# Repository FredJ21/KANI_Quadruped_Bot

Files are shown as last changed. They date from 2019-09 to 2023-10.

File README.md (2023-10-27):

# KANI_Quadruped_Bot
KANI - The quadruped bot

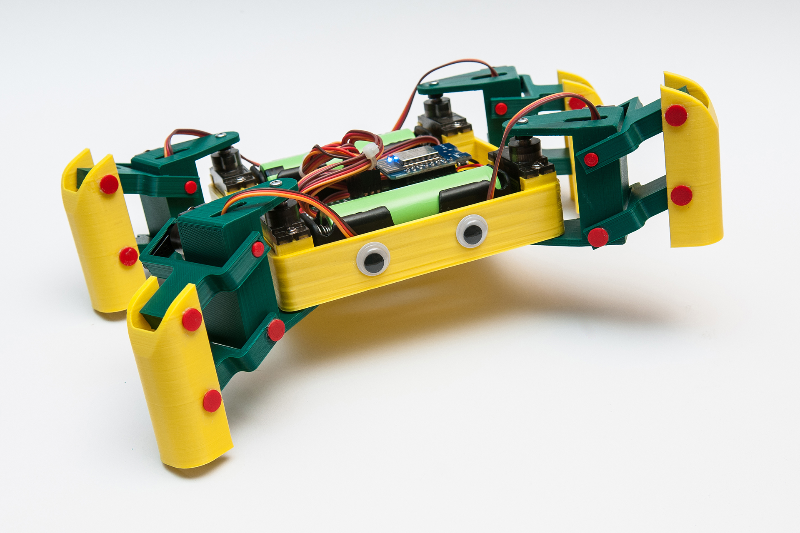
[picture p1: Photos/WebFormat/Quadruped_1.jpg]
KANI


KANI is a close cousin of KAME, another quadruped robot that we can discover here :  https://www.thingiverse.com/thing:1265766
 A big thank-you at bbq3D (https://www.thingiverse.com/bq3D/about) for his project and his inspiration.

But, KANI project is characterized by some interesting notes :

--> All the parts have been completely redesigned to facilitate 3D printing :
in PLA,

- without support structure,
- without adhesion border

--> The source files are available in the format :
- f3d  (Autodesk Fusion360)
- obj (3D format for import/export)
- stl (for 3D printing)

--> Any screws aren't needed for mounting articulation

--> The robot is designed around a ESP8266 and 8 servo motors type MG90S, in metal, robust and cheap

--> The set is powered by 2 batteries NCR18650B 3,7V 3400mAh and a 5V UBEC regulator

---
Update Sep. 2022 : BIG KANI - new version with MG996 servo

---
# On YouTube

<a href="https://youtu.be/avMEU6TQdt8">
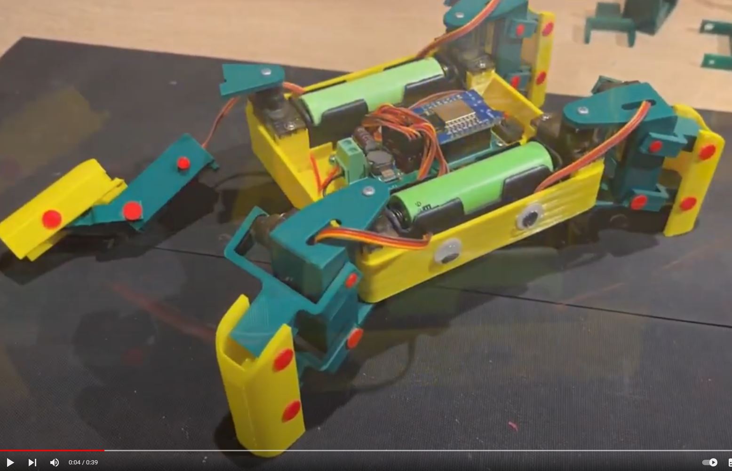
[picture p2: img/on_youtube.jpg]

</a>

https://youtu.be/avMEU6TQdt8

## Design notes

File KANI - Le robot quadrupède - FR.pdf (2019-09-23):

# KANI

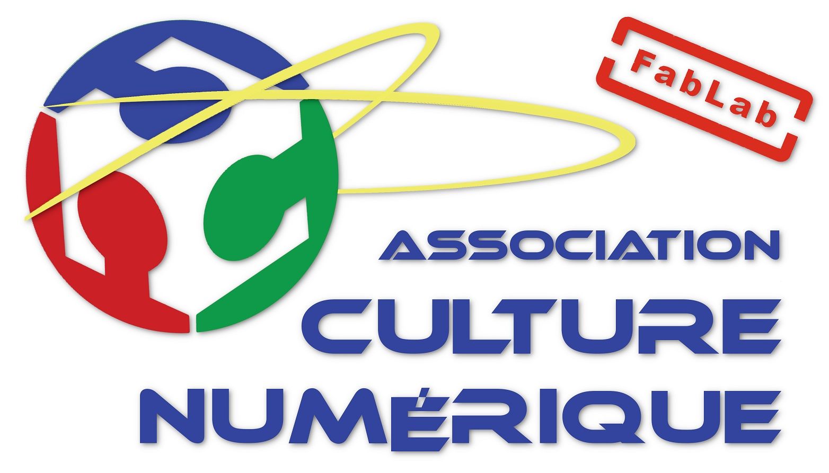
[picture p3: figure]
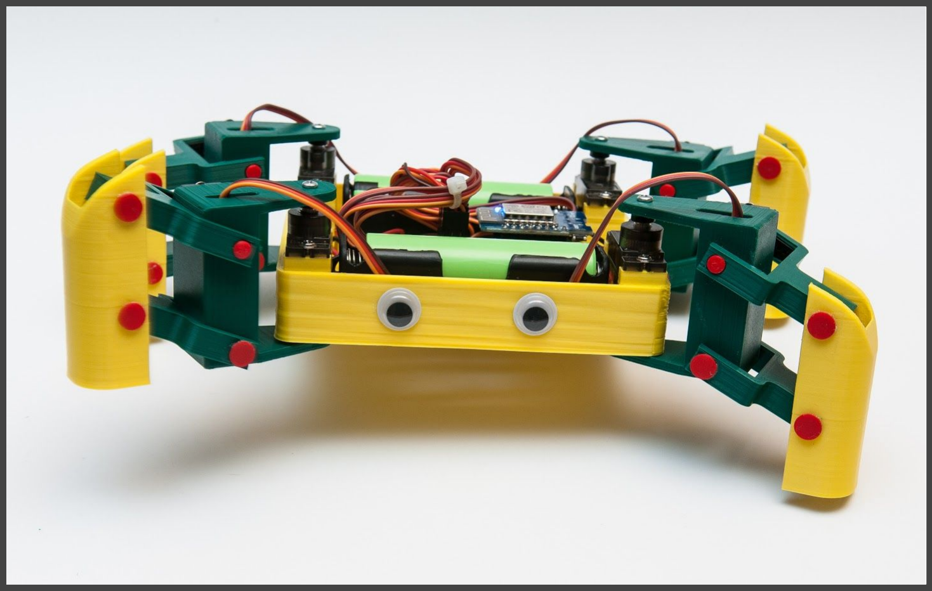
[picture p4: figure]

Le robot Quadrupède

Frédéric JELMONI
Septembre 2019

Version 1.0

# Sommaire

Présentation | 3
Réalisation des pièces mécaniques | 4
Liste des pièces | 4
Préparation des pièces | 5
Assemblage des jambes | 6
Réalisation Électronique | 8
Liste des pièces | 8
Schéma | 9
Réalisation du circuit | 10
Raccordement des moteurs | 11

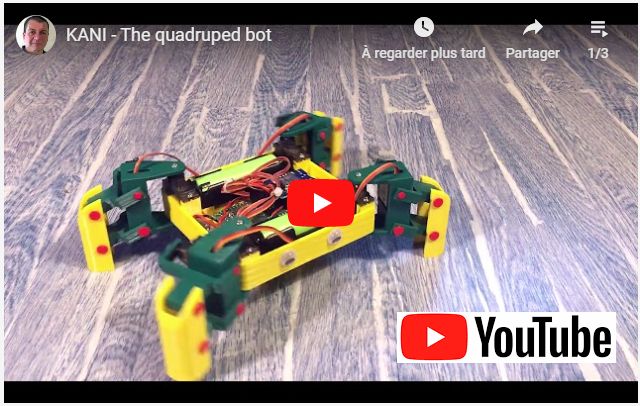
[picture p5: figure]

https://www.youtube.com/playlist?list=PLPA2ZF9G4l-84z5ALzUFqm6Zu1bBUUEop

### Présentation

KANI est un proche cousin de KAME, autre robot quadrupède que l’on peut découvrir ici : https://www.thingiverse.com/thing:1265766
Un grand merci à bq3D (https://www.thingiverse.com/bq3D/about) pour son projet et sa source d'inspiration.

Mais le projet KANI se caractérise par quelques points intéressants :

➔ l’ensemble des pièces à été complètement redessiné afin de faciliter l l’impression 3D :
- en PLA,
- sans structure de support,
- sans bordure d’adhérence

➔ les fichiers sources sont disponible au format :
- f3d (Autodesk Fusion360)
- obj (format 3D d’import/export)
- stl (pour l’impression 3D)

➔ Aucune vis n’est nécessaire pour le montage des articulations

➔ Le robot est conçu autour d’un ESP8266 et avec 8 servos moteurs de type MG90S, en métal, robustes et bon marché

➔ L’ensemble est alimenté par 2 batteries Lithium NCR18650B 3,7V 3400mAh et d’un régulateur 5V UBEC pour une autonomie de plus de 8 heures

L’ensemble de la documentation, fichiers 3D, code source, schémas, photos, est disponible ici : https://github.com/FredJ21/KANI_Quadruped_Bot

### Réalisation des pièces mécaniques

Les pièces mécaniques sont réalisées en impression 3D en PLA, sans structure de support et sans bordure d’adhérence.
Les axes d'assemblage sont également réalisés en impression 3D.

Les fichiers STL sont disponibles ici : https://www.thingiverse.com/thing:3874202

Liste des pièces

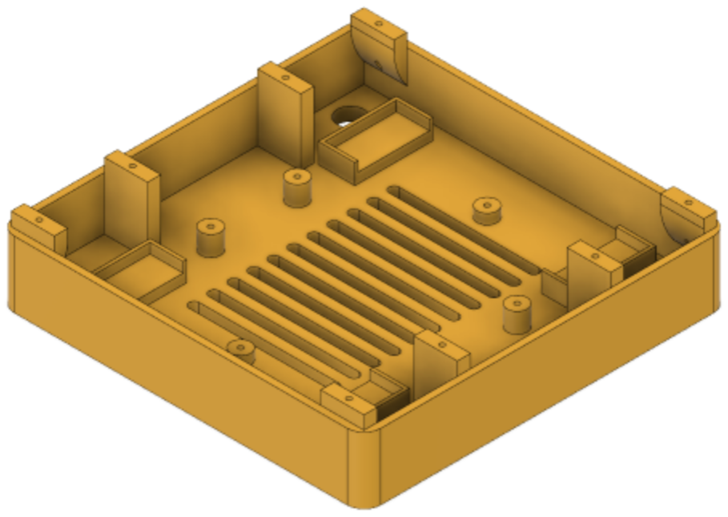
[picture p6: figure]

Corps
Fichier : Body.stl
Quantité : 1

Support de jambe 1
Fichier : Leg_support_1.stl Quantité : 2

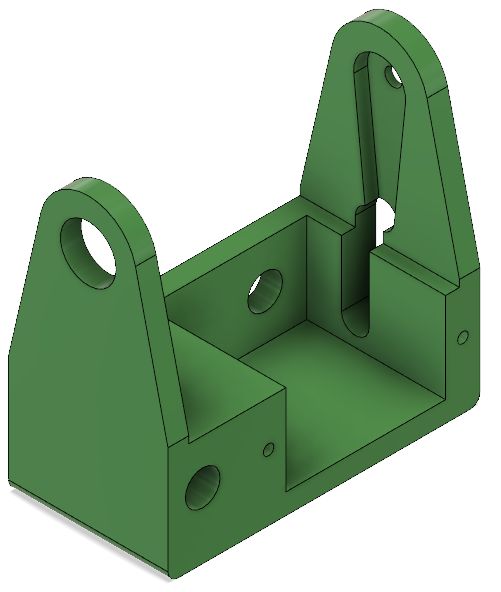
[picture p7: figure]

Support de jambe 2
Fichier : Leg_support_2.stl Quantité : 2

Articulation inférieure
Fichier : Lower_Articulation.stl Quantité : 4

Articulation supérieure
Fichier : Upper_Articulation.stl Quantité : 4

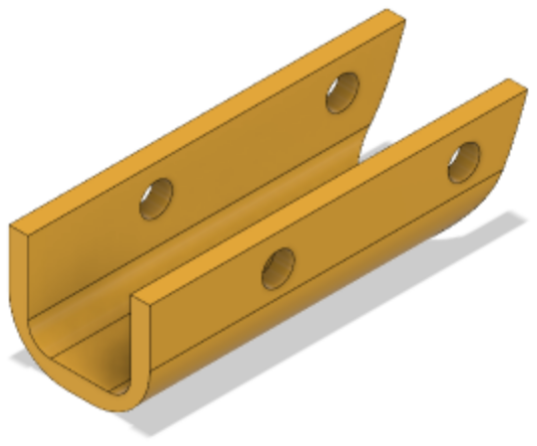
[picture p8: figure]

Jambe
Fichier : Leg.stl
Quantité : 4

Axe 8 mm
Fichier : Axle_8.stl
Quantité : 4

Axe 5 mm
Fichier : Axle_5.stl
Quantité : 28

Préparation des pièces

Afin d’obtenir une faible de résistance mécanique lors des mouvements des jambes, certaines pièces doivent être re-percées à l’aide d’un foret de 5 mm ou 8 mm.

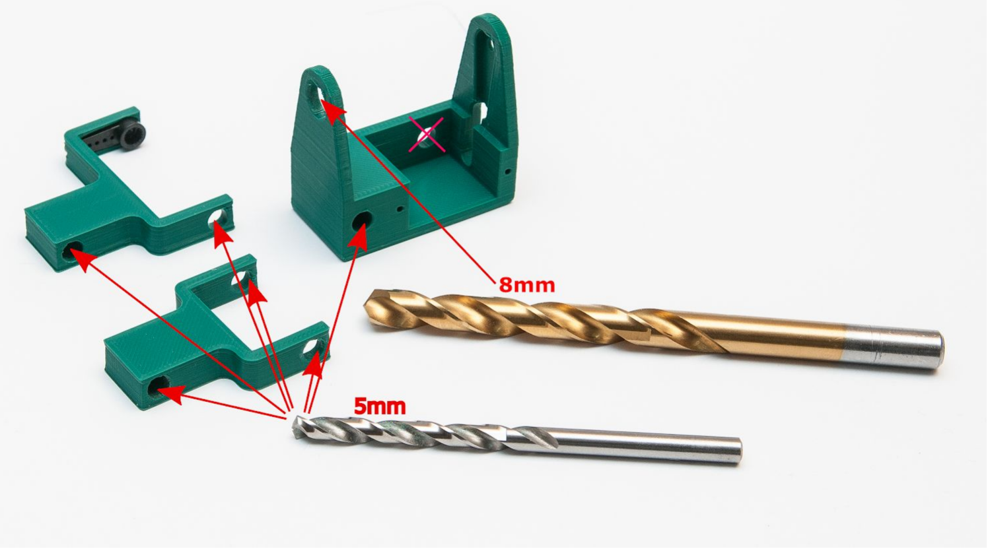
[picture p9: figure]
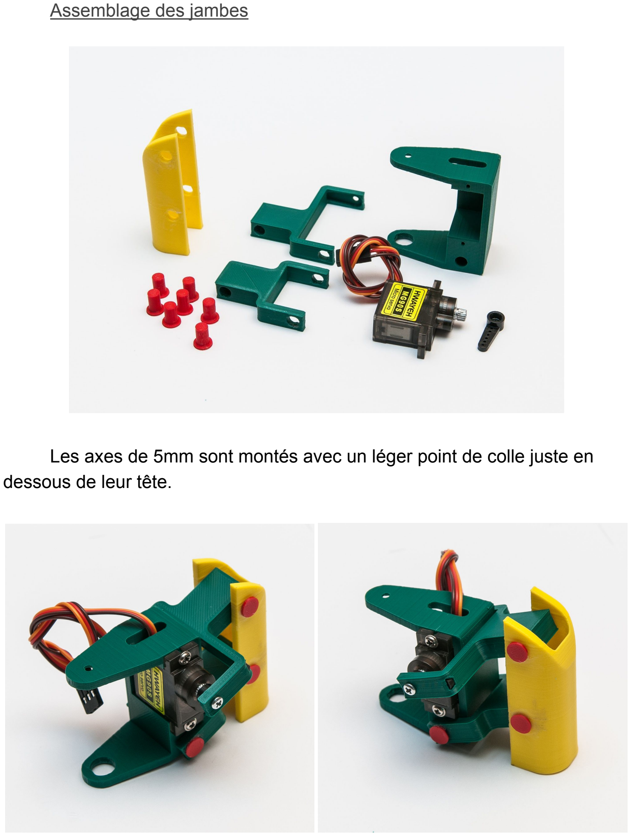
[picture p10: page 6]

Assemblage des jambes

Les axes de 5mm sont montés avec un léger point de colle juste en dessous de leur tête.

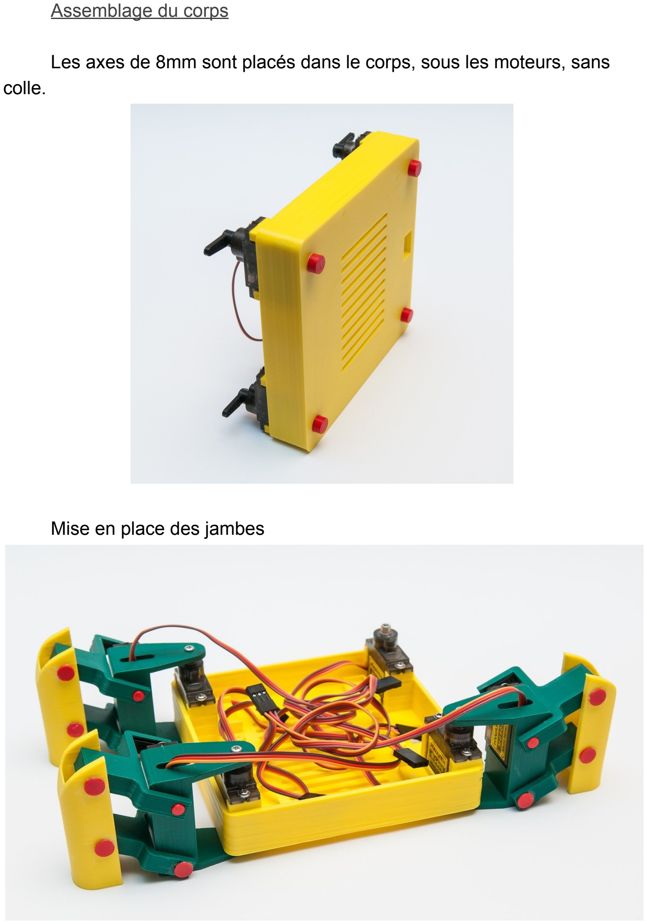
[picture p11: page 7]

Assemblage du corps

Les axes de 8mm sont placés dans le corps, sous les moteurs, sans colle.

Mise en place des jambes

### Réalisation Électronique

Liste des pièces

ESP8266 Wemos D1 Mini
https://fr.aliexpress.com/item/32651747570.html

### 8 Servo Moteur MG90S

https://fr.aliexpress.com/item/32970918454.html

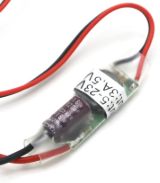
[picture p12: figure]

Régulateur UBEC 5v 3A
https://fr.aliexpress.com/item/32574612952.html

### 2 Supports de batteries 18650

https://fr.aliexpress.com/item/32847794157.html

PCB 3 x 7 cm
https://fr.aliexpress.com/item/32759438462.html

### 2 Batteries Lithium NCR18650B 3.7 v

3400mah
https://fr.aliexpress.com/item/32324914059.html

Schéma

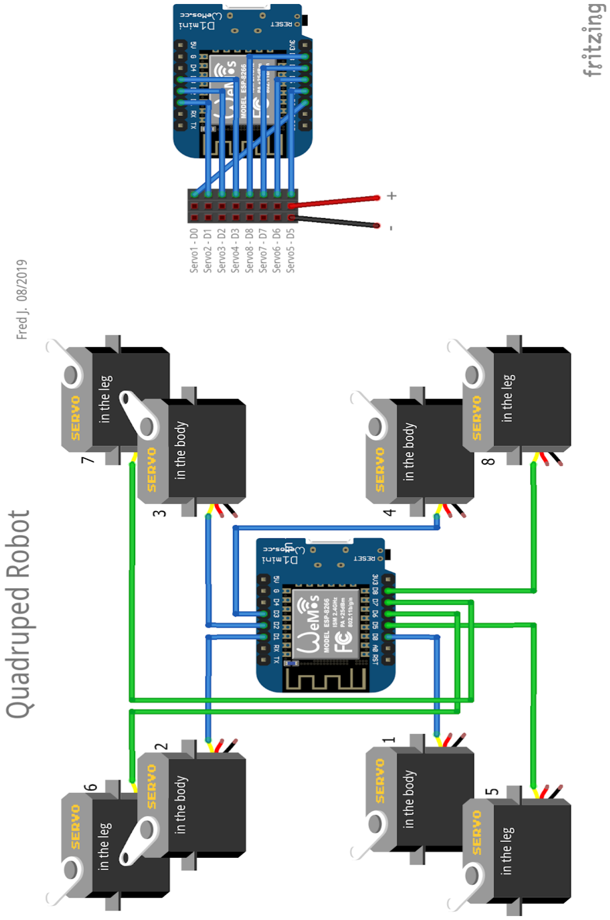
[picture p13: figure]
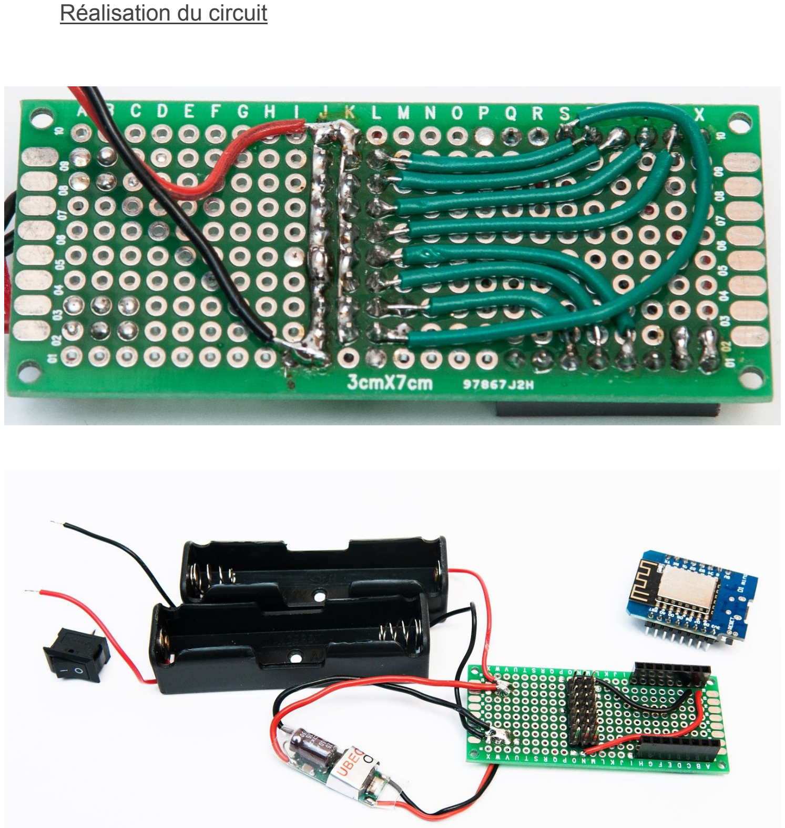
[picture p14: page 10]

Réalisation du circuit

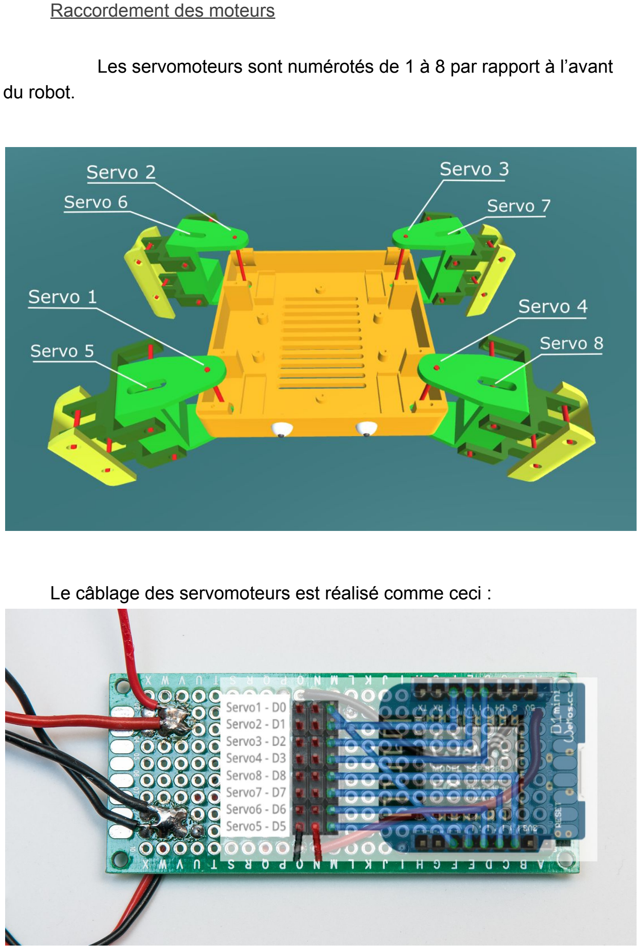
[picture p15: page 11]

Raccordement des moteurs

Les servomoteurs sont numérotés de 1 à 8 par rapport à l’avant du robot.

Le câblage des servomoteurs est réalisé comme ceci :

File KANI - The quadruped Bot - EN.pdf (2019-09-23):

# KANI


The Quadruped robot

Frédéric JELMONI
September 2019

Version 1.0

# Content

Introduction | 3
Realization of mechanical parts | 4
Parts list | 4
Preparation of parts | 5
Legs assembly | 6
Electronic Realization | 8
Parts list | 8
Diagram | 9
Realization of the circuit | 10
Motor connection | 11

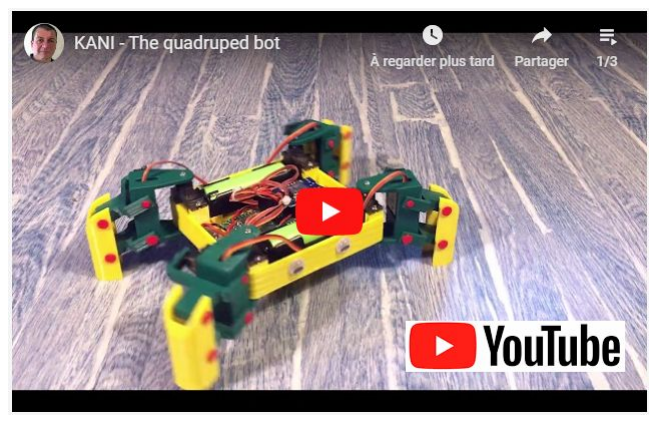
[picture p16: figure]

https://www.youtube.com/playlist?list=PLPA2ZF9G4l-84z5ALzUFqm6Zu1bBUUEop

Introduction

KANI is a close cousin of KAME, another quadruped robot that we can discover here : https://www.thingiverse.com/thing:1265766
A big thank-you at bbq3D (https://www.thingiverse.com/bq3D/about) for his project and his inspiration.

But, KANI project is characterized by some interesting notes :

➔ All the parts have been completely redesigned to facilitate 3D printing :
- in PLA,
- without support structure,
- without adhesion border

➔ The source files are available in the format :
- f3d (Autodesk Fusion360)
- obj (3D format for import/export)
- stl (for 3D printing)

➔ Any screws aren't needed for mounting articulation

➔ The robot is designed around a ESP8266 and 8 servo motors type MG90S, in metal, robust and cheap

➔ The set is powered by 2 Lithium battery NCR18650B 3,7V 3400mAh and a 5V UBEC regulator

All documentation, 3D files, source code, diagrams, photos, is available here : https://github.com/FredJ21/KANI_Quadruped_Bot

### Realization of mechanical parts

The mechanical parts are made of PLA 3D printing, without support structure and without adhesion border.
The assembly axes are also made in 3D printing.

STL files are available here: https://www.thingiverse.com/thing:3874202

Parts list


Body
File name: Body.stl
Quantity : 1

Leg support 1
File name: Leg_support_1.stl Quantity : 2


Leg support 2
File name: Leg_support_2.stl Quantity : 2

Lower articulation
File name: Lower_Articulation.stl Quantity : 4

Upper articulation
File name: Upper_Articulation.stl Quantity : 4


Leg
File name: Leg.stl
Quantity : 4

Axle 8 mm
File name: Axle_8.stl
Quantity : 4

Axle 5 mm
File name: Axle_5.stl
Quantity : 28

Preparation of parts

In order to obtain a low mechanical resistance during leg movements, some parts must be re-drilled using a 5 mm or 8 mm drill bit.

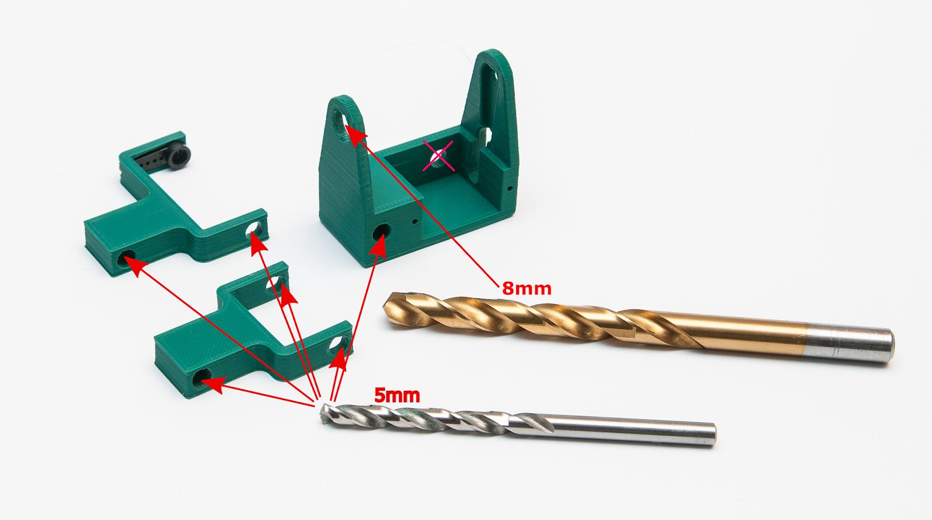
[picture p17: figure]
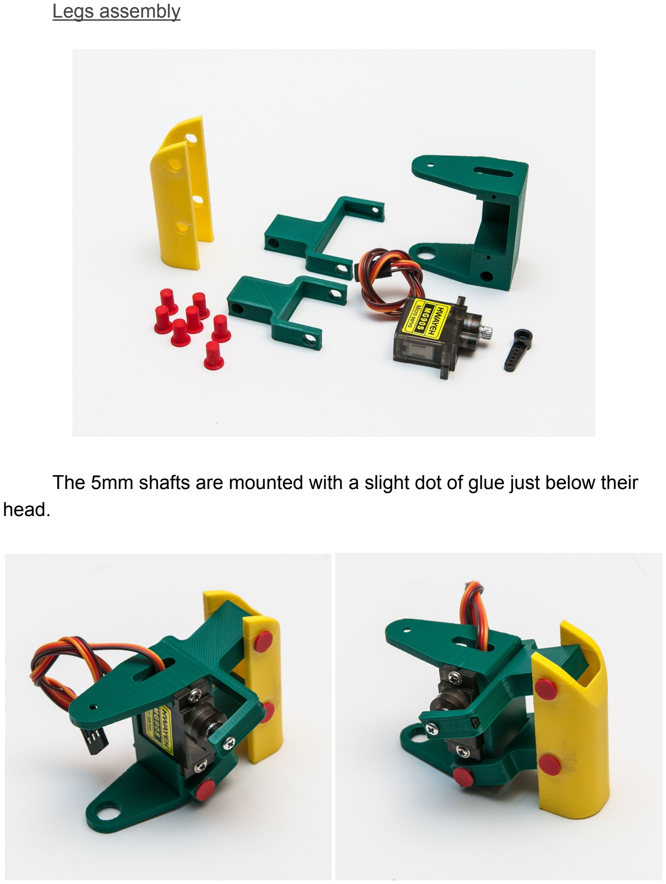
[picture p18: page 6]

Legs assembly

The 5mm shafts are mounted with a slight dot of glue just below their head.

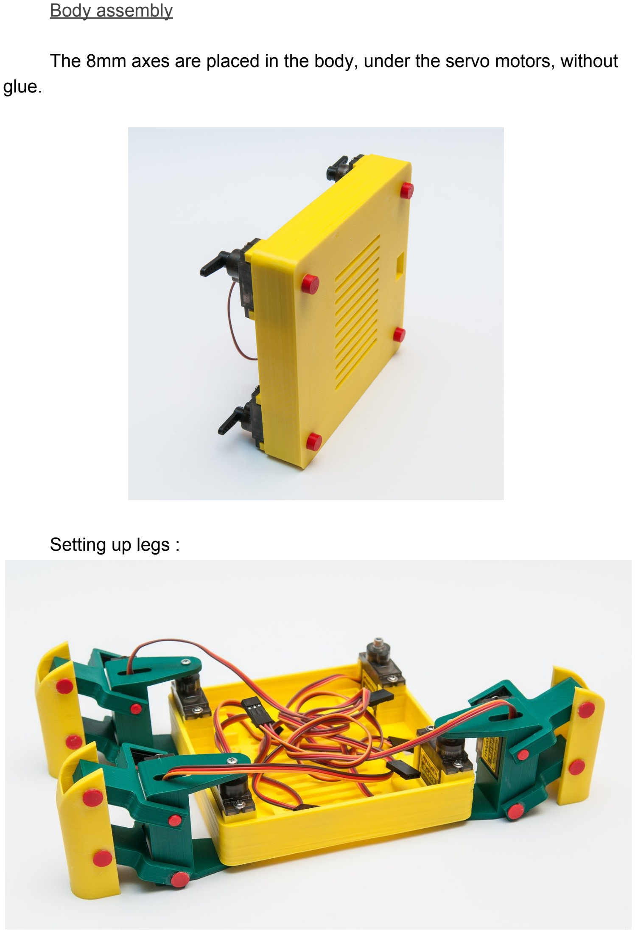
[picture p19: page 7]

Body assembly

The 8mm axes are placed in the body, under the servo motors, without glue.

Setting up legs :

### Electronic Realization

Parts list

ESP8266 Wemos D1 Mini
https://fr.aliexpress.com/item/32651747570.html

### 8 Servo Motors MG90S

https://fr.aliexpress.com/item/32970918454.html


Regulator UBEC 5v 3A
https://fr.aliexpress.com/item/32574612952.html

### 2 Battery holders 18650

https://fr.aliexpress.com/item/32847794157.html

PCB 3 x 7 cm
https://fr.aliexpress.com/item/32759438462.html

### 2 Battery Lithium NCR18650B 3.7 v

3400mah
https://fr.aliexpress.com/item/32324914059.html

Diagram

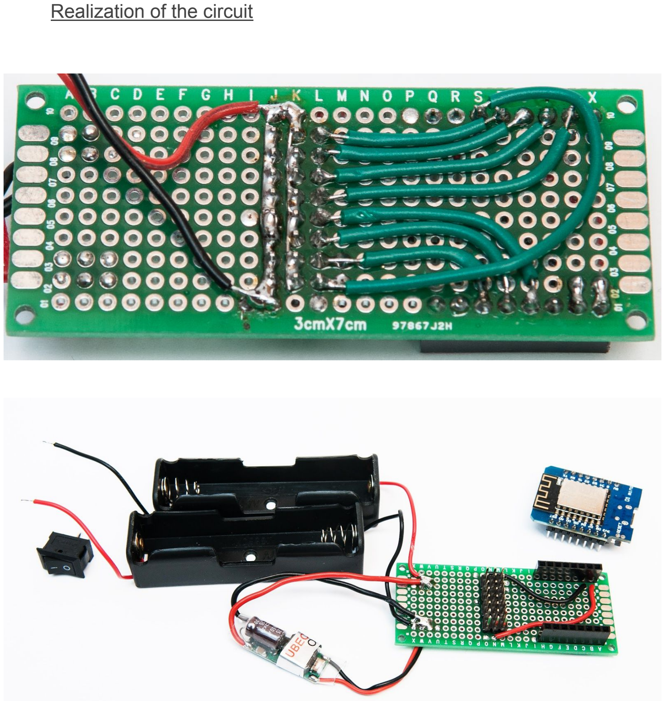
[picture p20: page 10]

Realization of the circuit

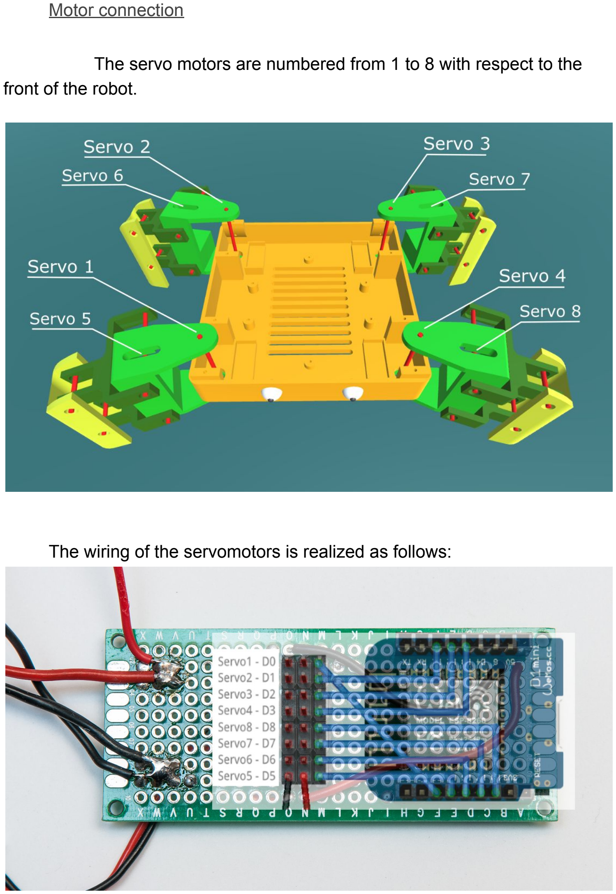
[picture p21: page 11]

Motor connection

The servo motors are numbered from 1 to 8 with respect to the front of the robot.

The wiring of the servomotors is realized as follows:

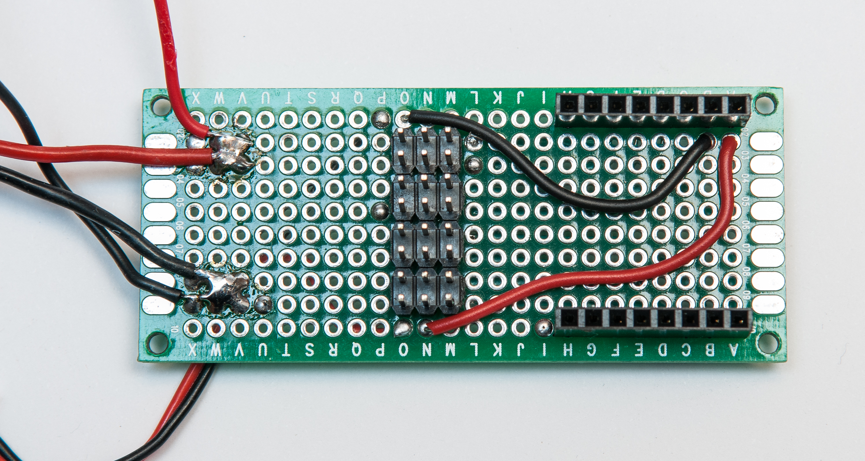
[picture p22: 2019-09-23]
Photos/1_Electronic_circuit_4.jpg

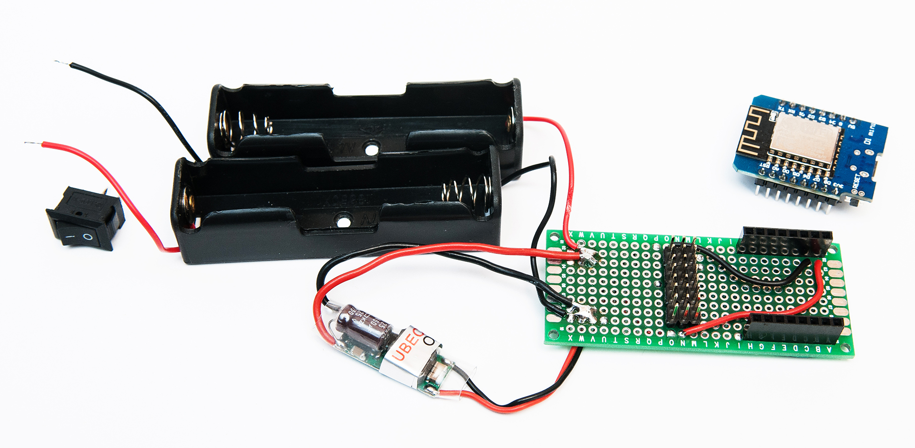
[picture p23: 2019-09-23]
Photos/WebFormat/1_Electronic_circuit_3.jpg

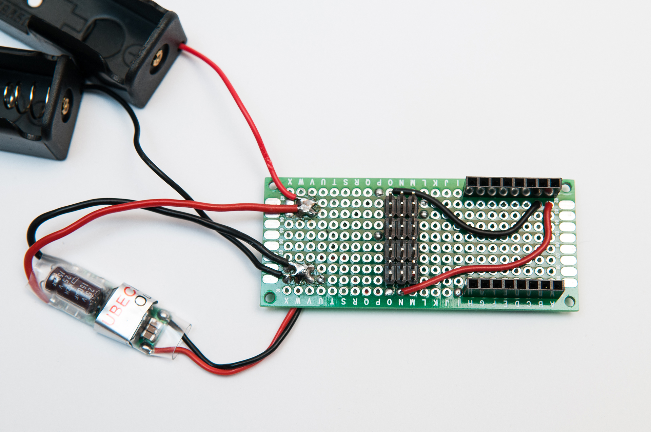
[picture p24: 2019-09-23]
Photos/WebFormat/1_Electronic_circuit_1.jpg

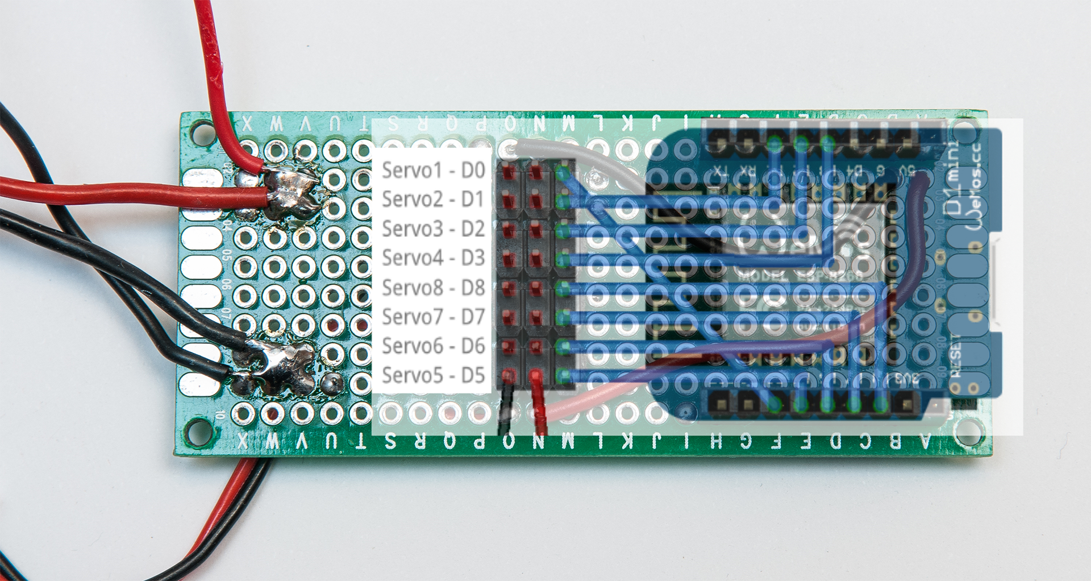
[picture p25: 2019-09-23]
Photos/WebFormat/1_Electronic_circuit_5.png

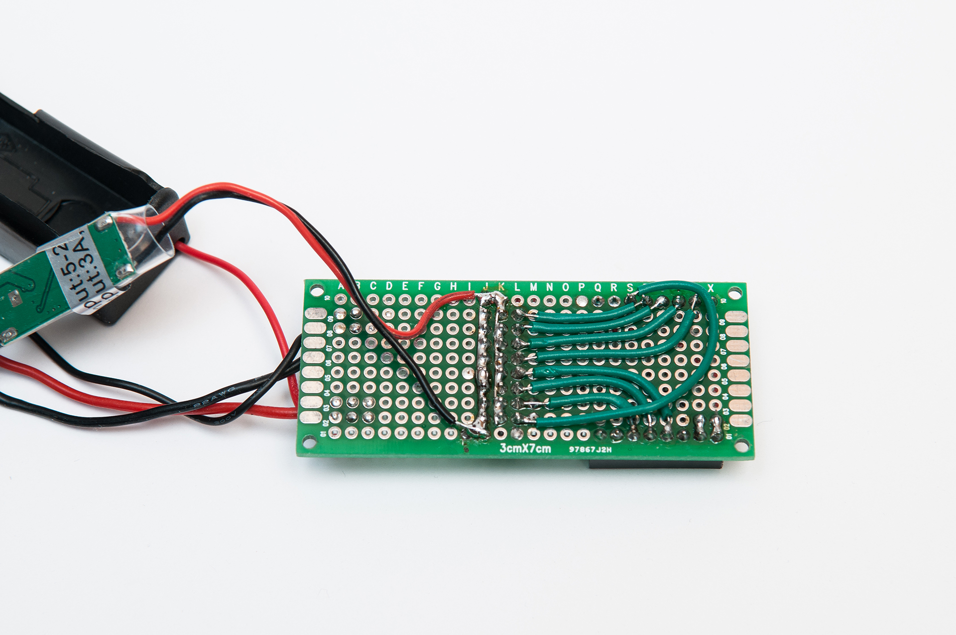
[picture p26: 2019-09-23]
Photos/WebFormat/1_Electronic_circuit_2.jpg

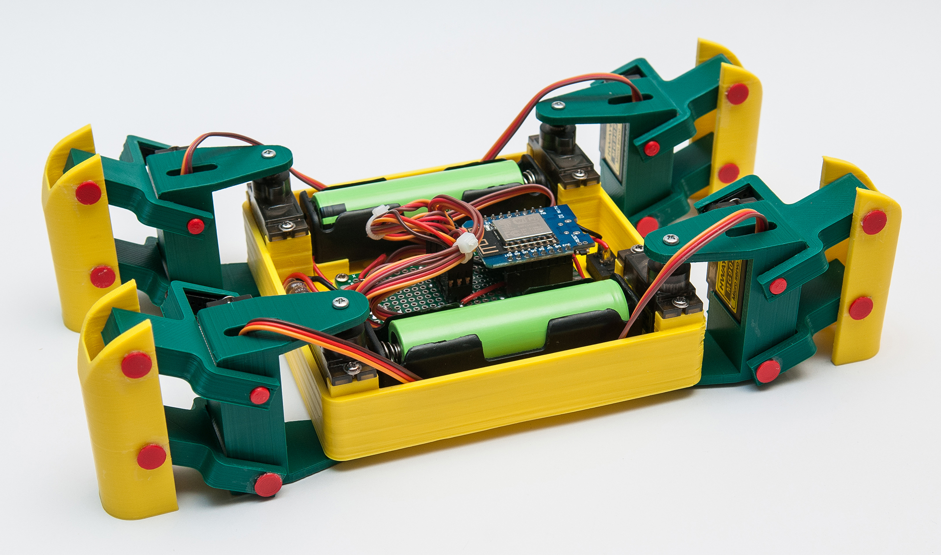
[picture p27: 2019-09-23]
Photos/WebFormat/4_Body_5.jpg

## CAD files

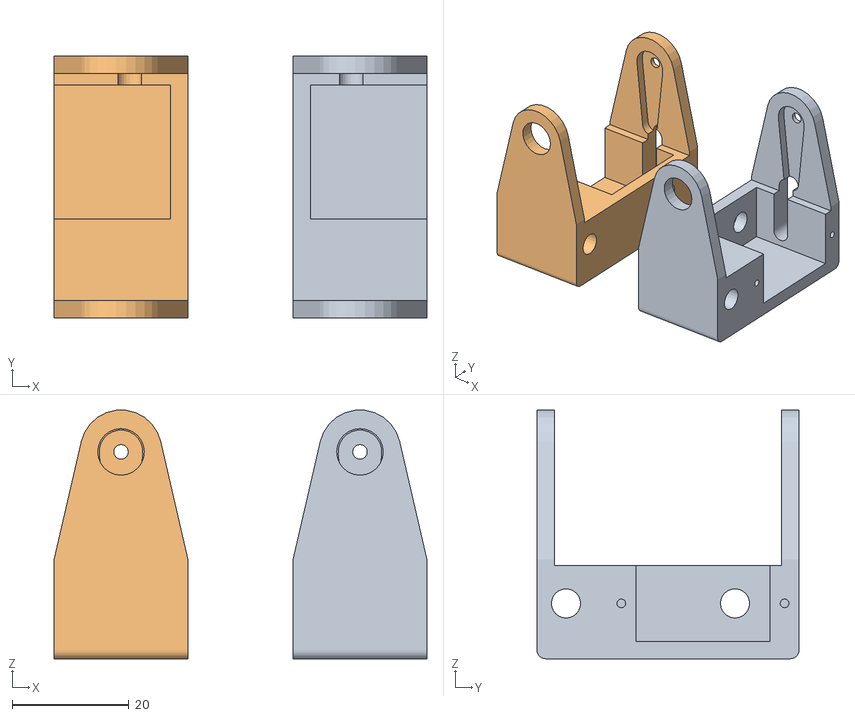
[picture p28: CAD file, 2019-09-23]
3D_Obj_files/Leg_support.obj
64.0 x 45.0 x 42.7
Avant_Bras_1
Avant_Bras_2

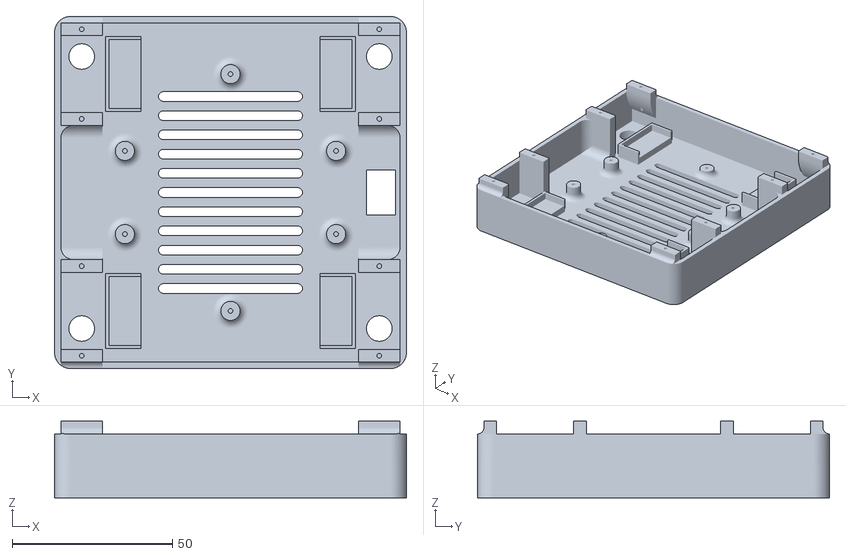
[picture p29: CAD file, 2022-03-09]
3D_Printing_STL_files/Body.stl
110.0 x 110.0 x 24.0

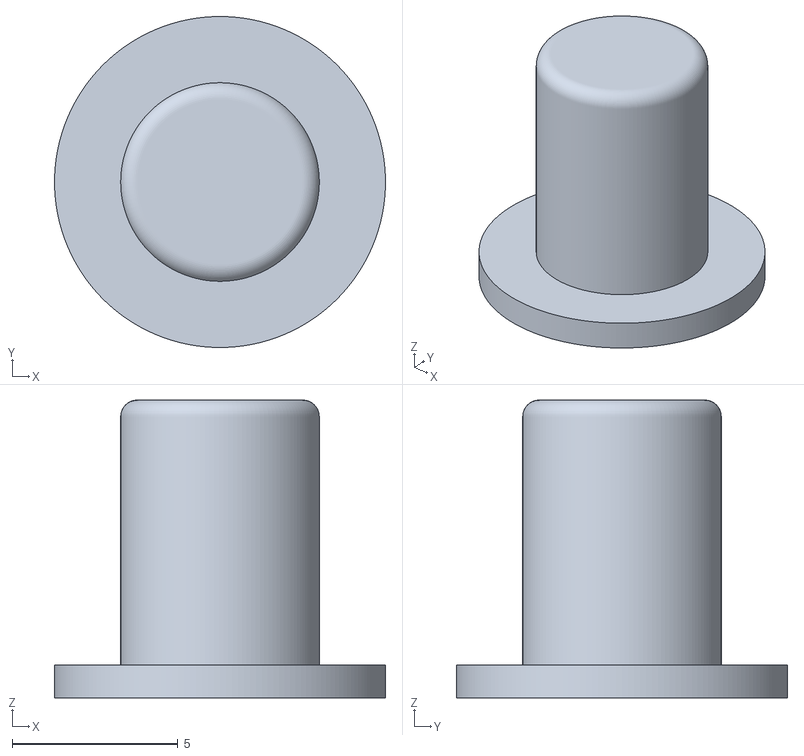
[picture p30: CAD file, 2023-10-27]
MG996_version/Axis_6.stl
10.0 x 10.0 x 9.00

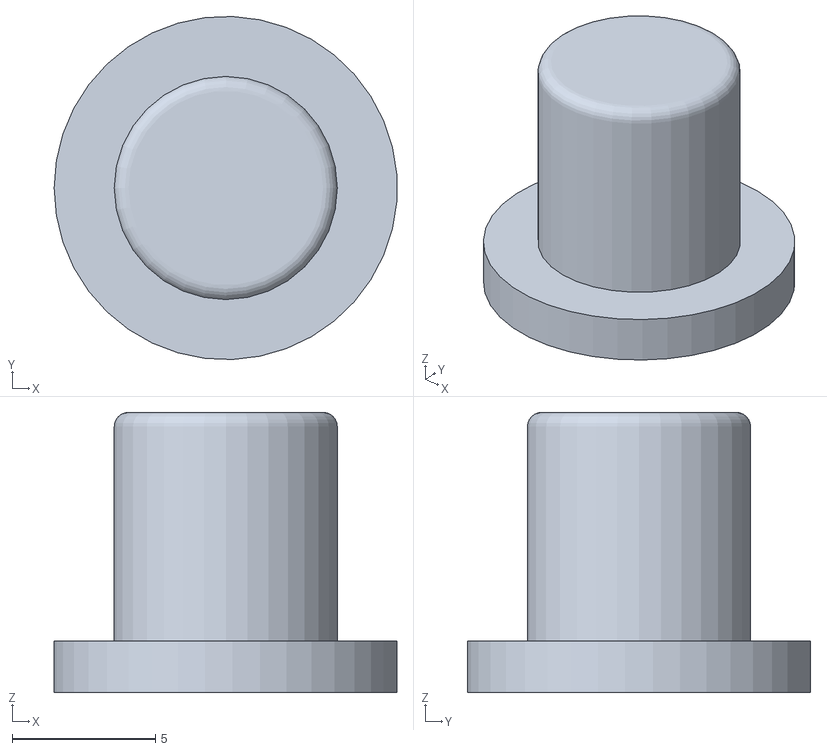
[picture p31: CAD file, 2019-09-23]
3D_Obj_files/Axle_8 v7.obj
12.0 x 12.0 x 9.80

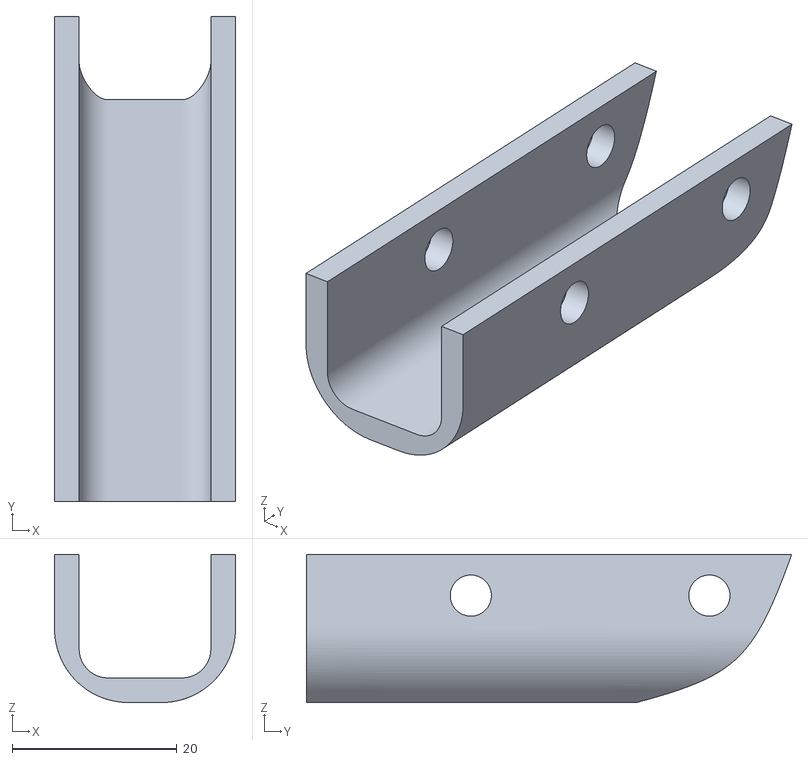
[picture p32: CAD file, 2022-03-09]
3D_Printing_STL_files/Leg.stl
22.0 x 59.0 x 18.0

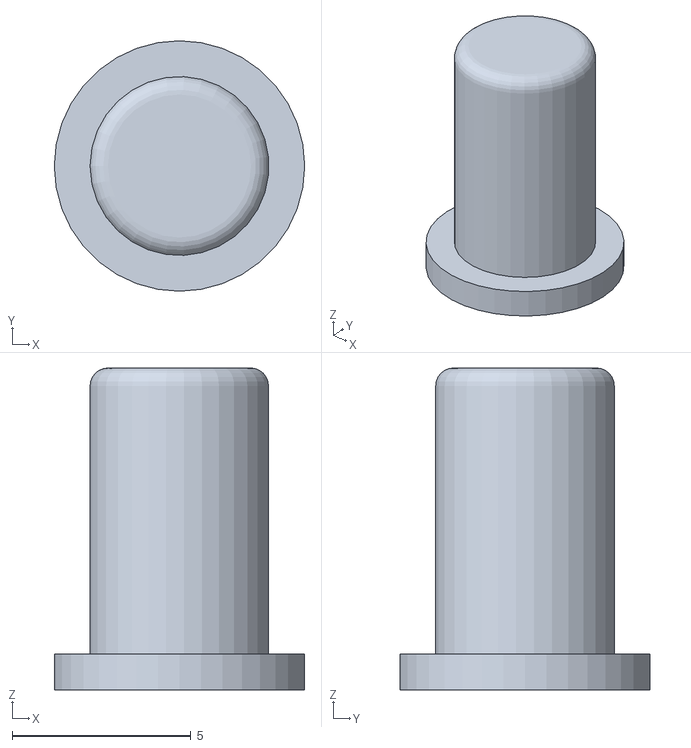
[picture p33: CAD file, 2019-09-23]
3D_Obj_files/Axle_5 v5.obj
7.00 x 7.00 x 9.00

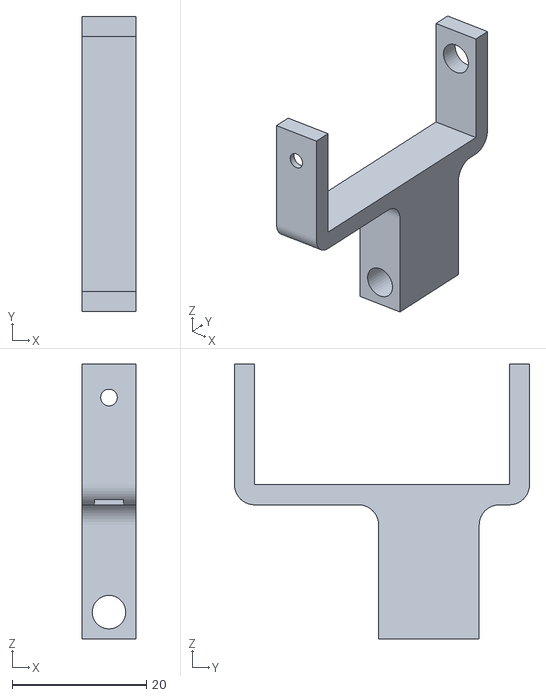
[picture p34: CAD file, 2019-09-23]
3D_Printing_STL_files/Upper_Articulation.stl
8.00 x 44.0 x 41.0

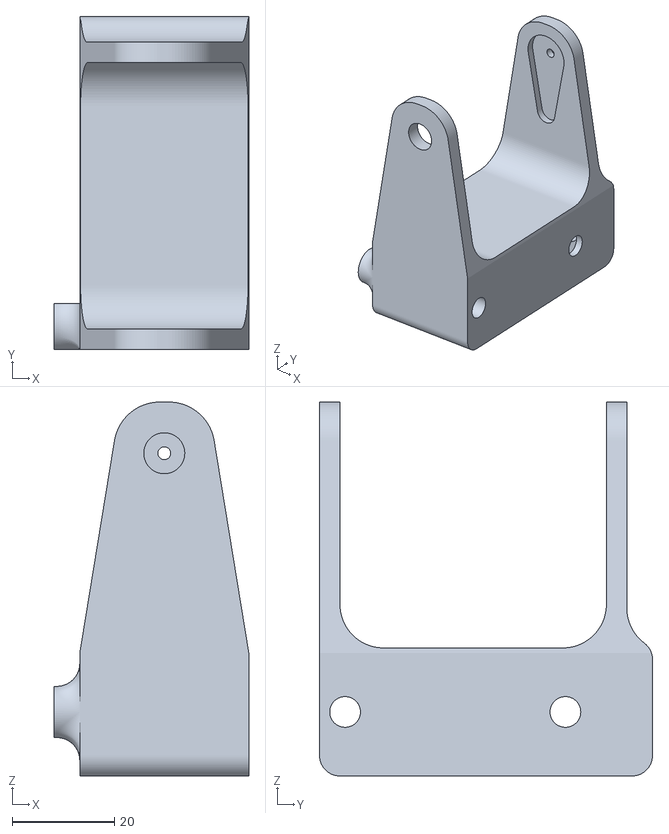
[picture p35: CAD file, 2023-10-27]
MG996_version/Avant_Bras_2.stl
38.0 x 65.0 x 73.0

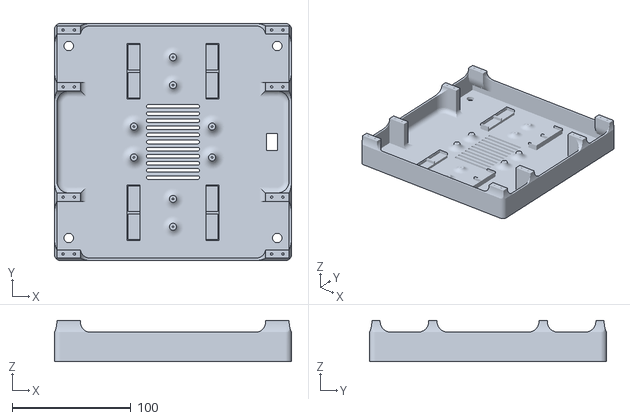
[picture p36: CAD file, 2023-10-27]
MG996_version/Quadruped_Body.stl
200.0 x 200.0 x 35.0

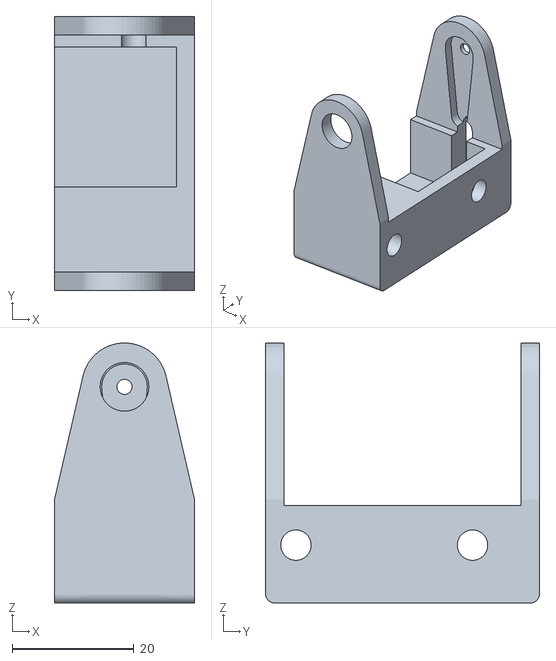
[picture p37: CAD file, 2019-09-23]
3D_Printing_STL_files/Leg_support_1.stl
23.0 x 45.0 x 42.7

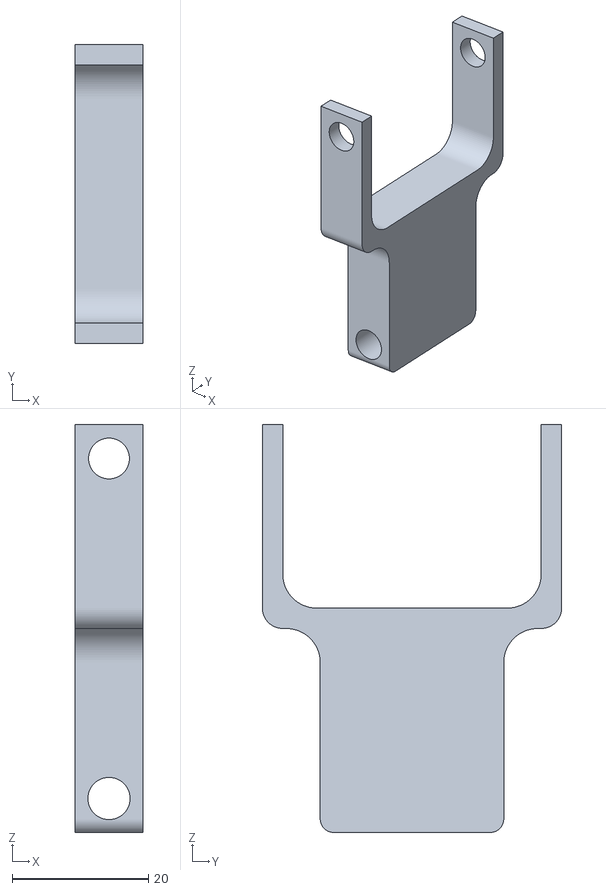
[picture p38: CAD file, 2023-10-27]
MG996_version/Lower.stl
10.0 x 44.0 x 60.0

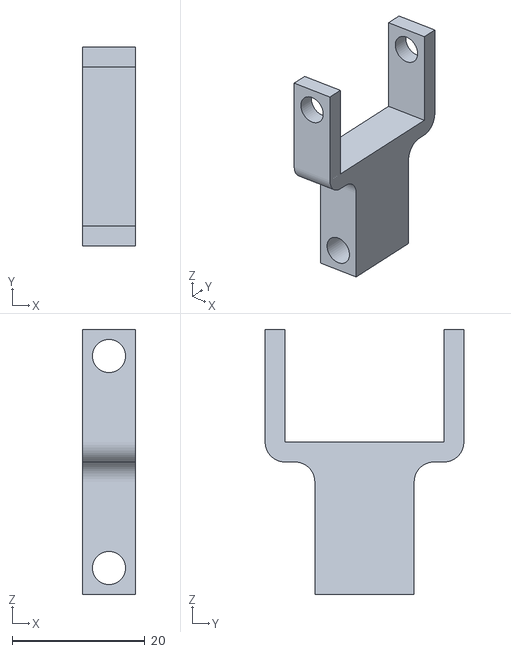
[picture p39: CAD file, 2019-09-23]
3D_Printing_STL_files/Lower_Articulation.stl
8.00 x 30.0 x 40.0

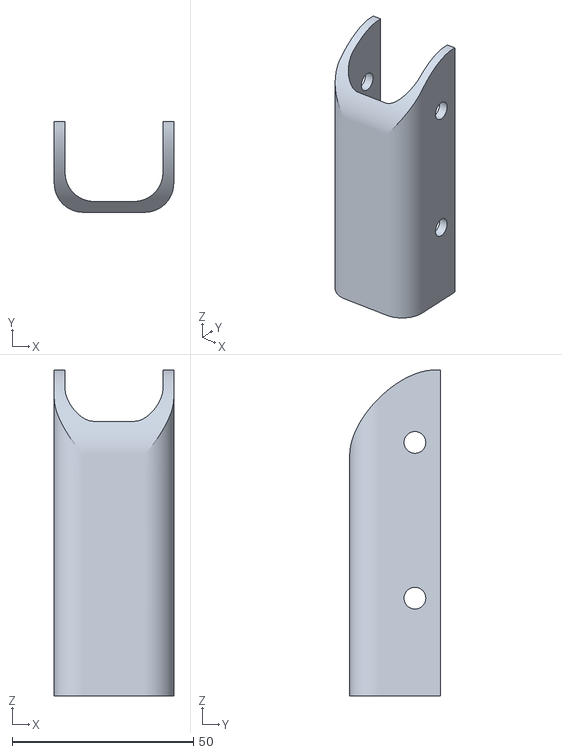
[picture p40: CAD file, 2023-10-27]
MG996_version/Leg.stl
33.0 x 25.0 x 90.0

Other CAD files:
MG996_version/Axis_8.stl
3D_Printing_STL_files/Axle_5.stl
MG996_version/Avant_Bras_1.stl
3D_Printing_STL_files/Axle_8.stl
3D_Printing_STL_files/Leg_support_2.stl
3D_Fusion360_sources/Axle_5.f3d
3D_Fusion360_sources/Axle_8.f3d
3D_Fusion360_sources/Body.f3d
3D_Fusion360_sources/Leg.f3d
3D_Fusion360_sources/Leg_support.f3d
3D_Fusion360_sources/Lower_Articulation.f3d
3D_Fusion360_sources/Upper_Articulation.f3d
3D_Obj_files/Body.obj
3D_Obj_files/Leg.obj
3D_Obj_files/Lower_Articulation.obj
3D_Obj_files/Upper_Articulation.obj
MG996_version/upper.stl

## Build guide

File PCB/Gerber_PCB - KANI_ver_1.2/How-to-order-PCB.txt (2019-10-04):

How to Order PCB

Please refer to:
https://docs.easyeda.com/en/PCB/Order-PCB

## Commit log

2019-09-23 Add schemas
    [Quadruped_Robot_Schema.fzz]
2019-09-23 Add 3D files
    [Axle_5 v5.obj, Axle_5.f3d, Axle_5.stl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]
2019-09-24 add PCB
2019-10-04 PCB ver 1.2 + photos
    [Gerber_BoardOutline.GKO, Gerber_BottomLayer.GBL, Gerber_BottomSilkLayer.GBO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]
2022-03-09 modify Body and add Prusa Gcode
    [Body.f3d, Body.obj, Body.stl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]
2022-09-05 Add MG996 version
    [Avant_Bras_1.stl, Avant_Bras_2.stl, Leg.stl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]
2023-10-27 Add Axis 6 & 8 in MG996 version
    [Axis_6.stl, Axis_8.stl]
